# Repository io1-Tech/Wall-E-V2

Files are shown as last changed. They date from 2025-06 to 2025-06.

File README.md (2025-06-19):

# Wall · E V2

This is my personal project, Wall-E, a robot I designed and built from scratch.

It includes electronics, 3D printed parts, servo motors, sound, a laser, and a taser system (for fun). I made everything myself.

Wall-E Robot

## 📦 Project Contents

- `code/`: Arduino code (multiple versions)
- `schematics/`: Schematics, diagrams, and professional circuits
- `3d_models/`: 3D printed designs
- `photos/`: High quality photos of the project
- `sounds/`: Audio effects used in the robot
- `libraries/`: Arduino libraries used in the code
- `components/`: Full Component List

## 🕹️ Control System

This robot can be controlled using:
- Xbox Controller (Bluetooth)
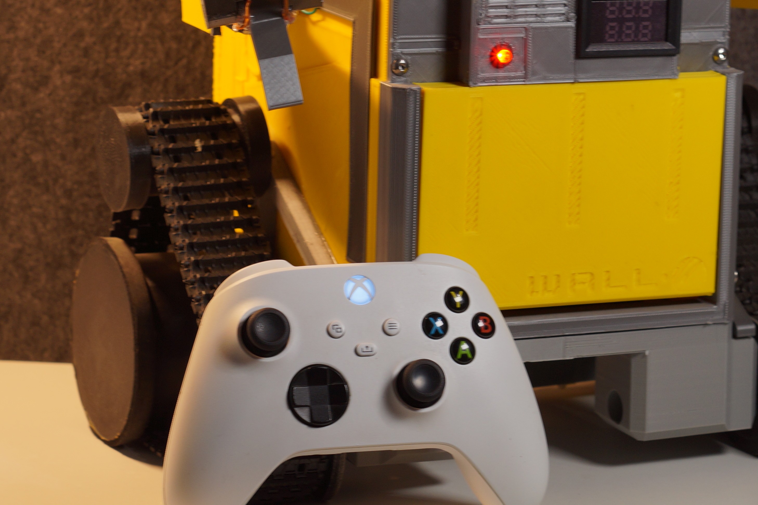
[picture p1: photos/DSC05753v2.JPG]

- Remote XY App (previous versions)
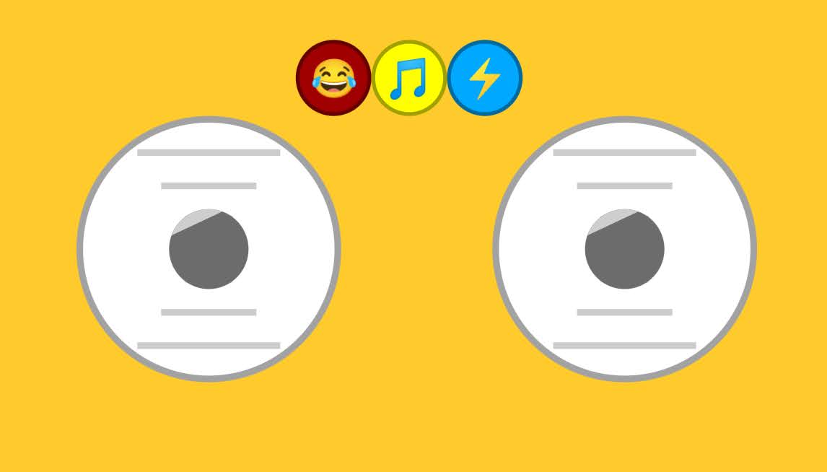
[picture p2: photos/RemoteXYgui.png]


## 🔩 Full Component List

You can find a complete, organized list of all electronic, mechanical, and auxiliary components used in this project in the spreadsheet below:

📄 [Wall-E-V2_components_list.xlsx](components/Wall-E-V2_components_list.xlsx)

This table includes:
- Quantity and part numbers  
- Technical specifications  
- Purpose in project  
- Reason for selection  
- Reference images  

Also i made a schematic with all the conections
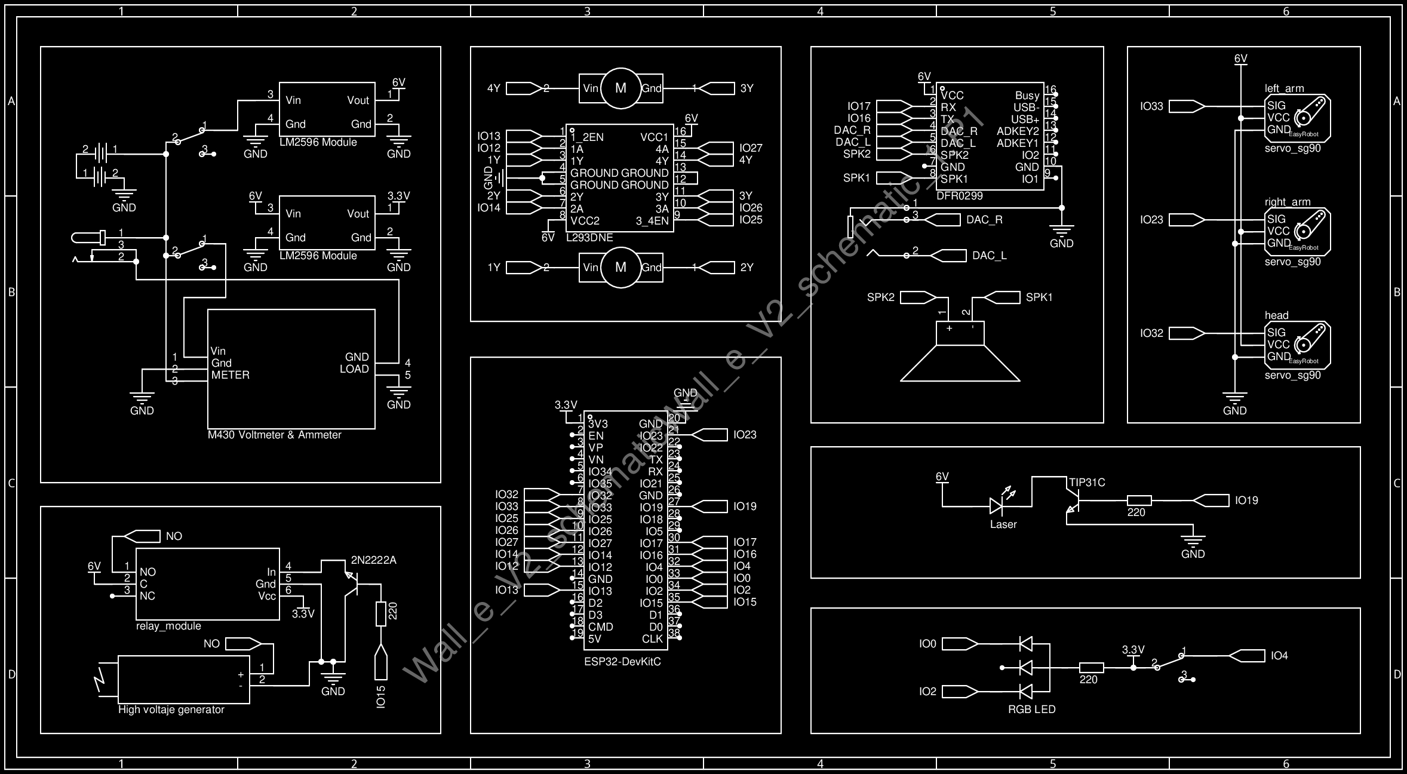
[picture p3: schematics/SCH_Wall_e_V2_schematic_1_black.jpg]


## 🛠️ Tools and Platforms Used

Here’s a list of the main tools and platforms I used throughout the WALL·E project:

- **Fusion 360** – Designed 3D parts of the robot and exported STL files for 3D printing.
- **Fritzing** – Simulated circuits and verified wiring before building the physical prototype.
- **EasyEDA** – Created professional circuit schematics and organized the wiring logic.
- **Arduino IDE** – Developed and uploaded firmware to the ESP32 microcontroller.
- **GitHub** – Used for version control, documentation, and collaboration.
- **OrcaSlicer** – Used slicing all my 3d printabled parts.

## 📸 Preview

Wall-E Robot
Wall-E Robot
Wall-E Robot
Wall-E Robot

## 📂 Version History

- v1.0: Basic control and movement
- v2.8: Bluetooth control with Remote XY
- v3.4: Xbox Controller and sound system added (FINAL VERSION)

## 🧠 Author

Created by: io1

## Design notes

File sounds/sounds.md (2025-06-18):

Place these MP3 files onto a microSD card. Insert the card into the DFPlayer module to enable audio playback in your project.

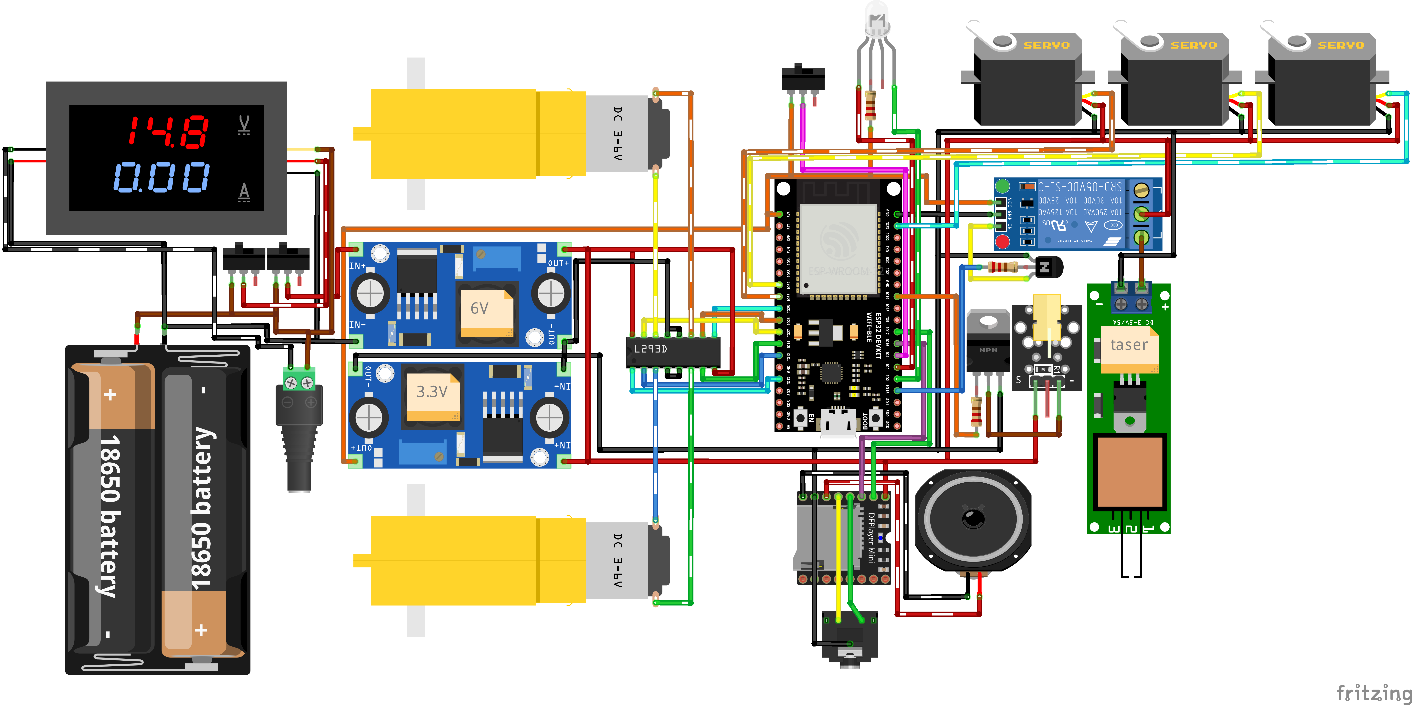
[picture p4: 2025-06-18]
schematics/Fritzing_SCH_Wall_e_V2_schematic.png

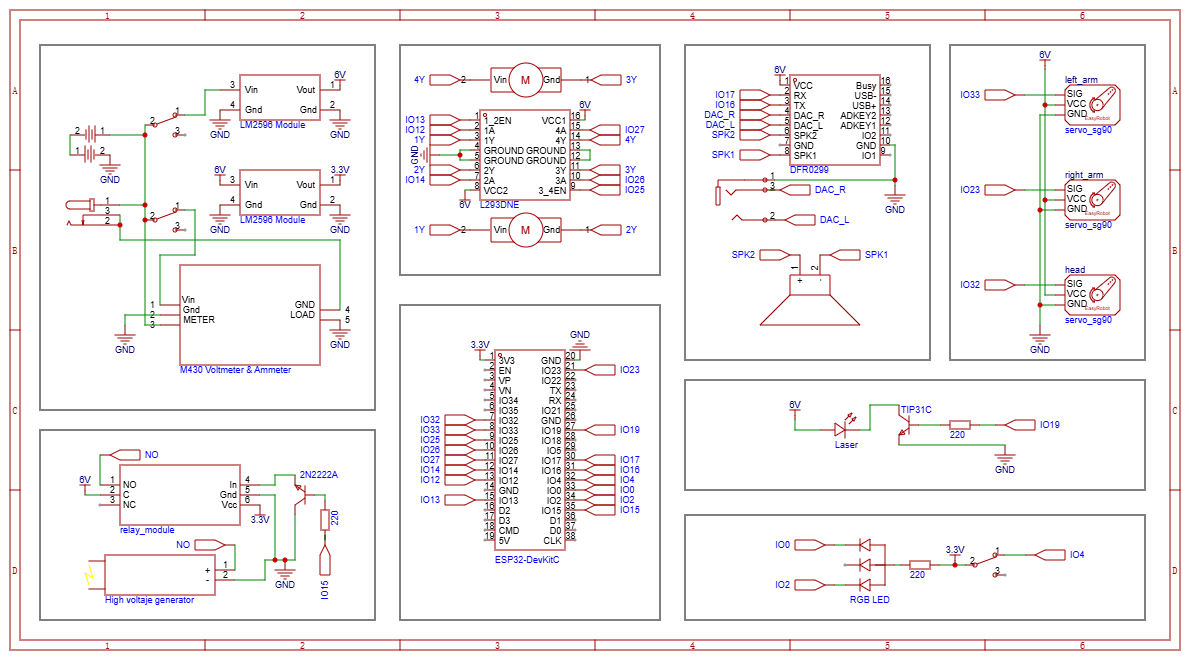
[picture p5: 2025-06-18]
schematics/SCH_Wall_e_V2_schematic_1_normal.png

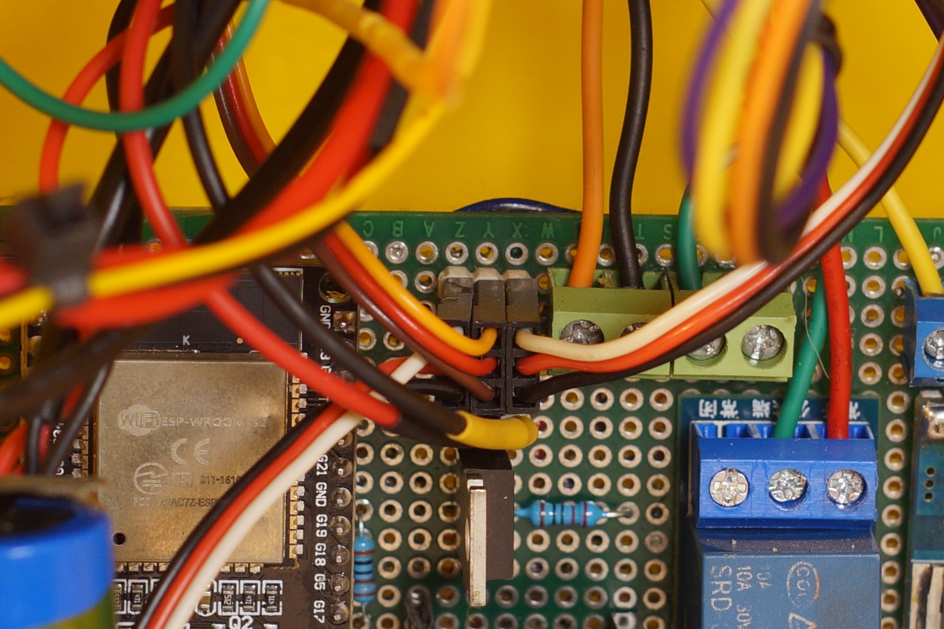
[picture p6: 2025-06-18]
photos/DSC06053v2.JPG

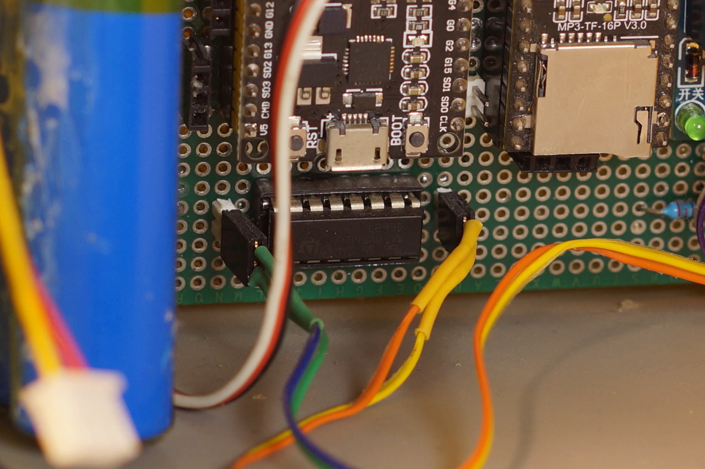
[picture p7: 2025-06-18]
photos/DSC06054v2.JPG

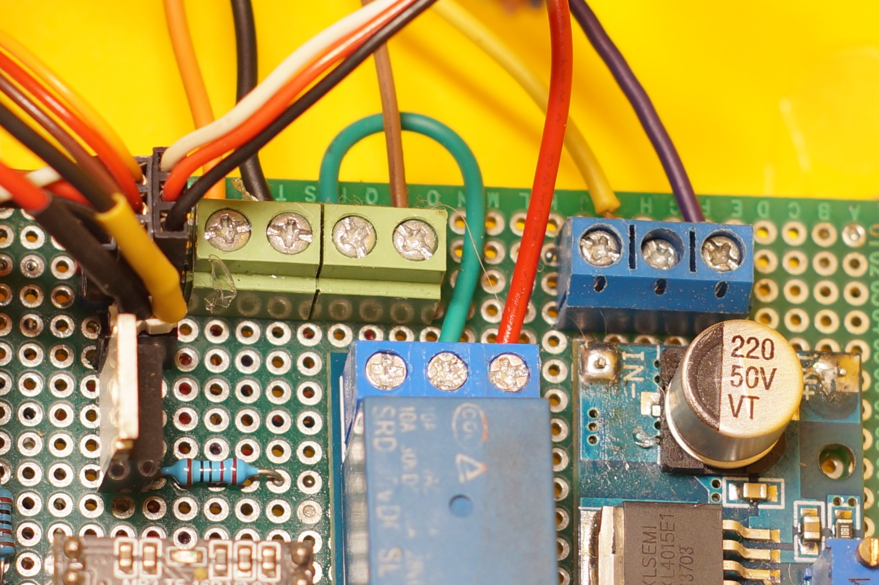
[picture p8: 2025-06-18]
photos/DSC06059v2.JPG

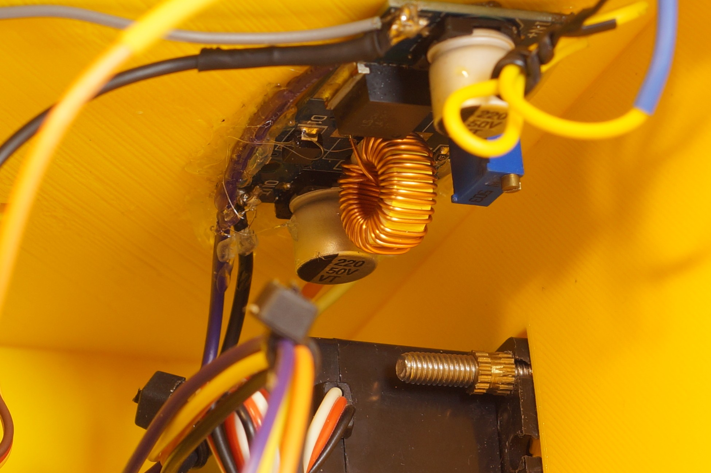
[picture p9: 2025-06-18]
photos/DSC06058v2.JPG

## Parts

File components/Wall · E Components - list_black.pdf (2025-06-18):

# Wall · E Components

Hardware Components | June 2024 | io1 🔩 | Electronics & Control No QTY Component | Description | Function in Project | Why This Component? | Photo

### 1 x1

### ESP-WROOM-32 Dev Board 38pins

Dual-core microcontroller with Wi-Fi & Bluetooth by Espressif. Acts as the central processing unit for all logic, communication, and control tasks.

Acts as the brain of the robot, managing sensor input, motor control, communication, and

logic.

Chosen for its wireless capabilities, performance, and large community. Ideal for embedded robotics.

### 2 x1

### Double H-bridge L293 DIP-16

Dual H-Bridge motor driver capable of driving two DC motors or one stepper motor. Supports bidirectional control.

Drives the left and right DC motors to enable robot

locomotion.

Simple integration with microcontrollers, handles small DC motors efficiently.

### 3 x1

### TIP31C & 2N2222 Transistors

TIP31C: Medium-power NPN BJT, rated for 3A collector current, 40V Vce. 2N2222: Low-power NPN BJT with 800mA max current and fast switching.

TIP31C: Used as a switch for the laser. Receives signal from ESP32 and allows higher current to activate the laser safely. 2N2222: Used to switch the relay for the Taser. Prevented dangerous startup behavior by blocking

Allows safe control of higher loads using GPIO signals.

### 4 x1

### 5V Relay Module (1 channel)

Electromechanical switch that isolates and controls high-voltage circuits using low-voltage control.

Activates the Taser circuit when triggered.

Ensures electrical safety and modularity. Initially problematic, later replaced by transistor system.

### 5 x2

### LM2596 Step- Down Regulator

Step-down voltage regulator, input up

to 35V, output adjustable, 3A max. | Converts 7.4V from battery to 3.3V for logic-level devices and 6V to Motors and High Voltaje Generator

Maintains stable 3.3V for ESP32 and logic circuits from 7.4V Li-ion pack.

### 6 x1

### High Voltage Generator (Taser)

Generates high-voltage pulses (~10kV)

Powers the simulated “Taser” mechanism in the arm. | Mainly for curiosity and add a funny touch :)
🔋 | Power System
No QTY Component | Description | Function in Project | Why This Component? | Photo

### 7 x1

### 18650 Battery Pack (2S1P, 7.4V

### 2200mAh)

Rechargeable lithium-ion battery pack configured as 2 cells in series for 7.4V output.

Provides main power supply for motors, logic, and peripherals.

Provides sufficient capacity and current for both logic and motors.

### 8 x1

### 1A 8.4V Charger

Standard Li-ion battery charger for 2S
(7.4V) configurations. | Recharges the main battery pack. | Matched to battery chemistry and voltage.

### 9 x1

### M430 Voltmeter & Ammeter

Measures and displays real-time voltage and current of the power supply.

Monitors battery status and power draw.

Prevents undervoltage and ensures safe operation.

⚙ | Mechanical Actuation & Movement No QTY Component | Description | Function in Project | Why This Component? | Photo

10

### SG90 Micro Servo (Head)

Compact analog servo with ~180° movement range, low power consumption.

Controls lightweight parts like the neck articulation.

Budget-friendly and sufficient for one head. Future upgrade required.

11

### MG996R Servo (Arms)

High-torque digital servo with metal gears, rotation of ~180°, operating at 4.8–7.2V.

Controls the arm movement

for expression and motion. Chosen for torque, accessibility and capacity, though near operational limit. Future upgrade required.

12

### Yellow Gear Motors (L-shaped)

Main movement system | Main movement system. Future upgrade required.

Low-cost motors with adequate torque. Limited for heavy load.

13

### Plastic Track System

Pre-assembled plastic track mechanism with wheels.

Provides traction, but due to poor fit, not fully
functional.

Bought pre-assembled for ease; unfortunately, poorly designed, with wheels often slipping out.

🖌 | 3D Design & Materials
No QTY Component | Description | Function in Project | Why This Component? | Photo

14

### Fusion 360 Design

Autodesk Fusion is a commercial computer-aided design (CAD), has built-in capabilities for 3D modeling, collaboration, simulation and documentation.

Used to Design WALL·E’s body, arms, and head components.

Ensures accurate fit, modularity, and presentation quality.

15

### PLA Filament

(Black, Yellow,

### Silver)

Thermoplastic material used for 3D printing parts. | Used to print WALL·E’s body, arms, and head components.

Lightweight, good finish, and easy to post- process.

16

### M4 Brass Inserts

Brass components used to reinforce screw holes in 3D printed parts. Provides stronger and
reusable screw threading in PLA pieces.

Avoids plastic cracking and adds professionalism.

💡 | Auxiliary & Visual Effects
No QTY Component | Description | Function in Project | Why This Component? | Photo

17

### DFPlayer Mini

MP3 audio playback module with onboard microSD and speaker support.

Plays sound effects or voice commands from WALL·E.

Allows autonomous sound effects stored on microSD.

18

### 5mm Laser Diode (Red)

Compact red diode laser module operating at 5V.

Aesthetic effect used in the arm for visual targeting. Aesthetic enhancement and directional indicator.

19

### RGB LED (Common Anode)

Multi-color LED with 4 pins: one common anode and R/G/B cathodes.

Indicates Safe mode, green for safe, red for taser activated

For simplicity and a lot of documentation online

### 20 x3

### DPDT Switch

Double Pole Double Throw switch with two stable ON states.

Ensures manual override for safe operation.

A classic Switch

21

### 4Ohm 3W speaker

Audio playback speaker, conected to DF player mini

Audio output for Sound effects and music | Maximum power and resistance supported by the DF player mini

22

### Xbox Series Controller

Wireless Bluetooth gamepad compatible with ESP32 via BLE. Offers analog and digital input.

Used as the remote controller to wirelessly operate WALL·E's movement and

features.

Chosen for its BLE compatibility, precision, and ergonomic design. Easy to integrate and

intuitive for real-time control.

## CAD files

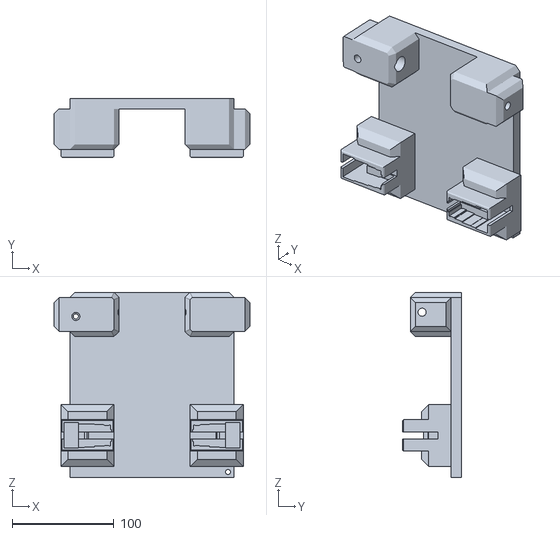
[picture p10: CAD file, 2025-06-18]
3d_models/stl files/Down_side.stl
192.5 x 57.6 x 182.0

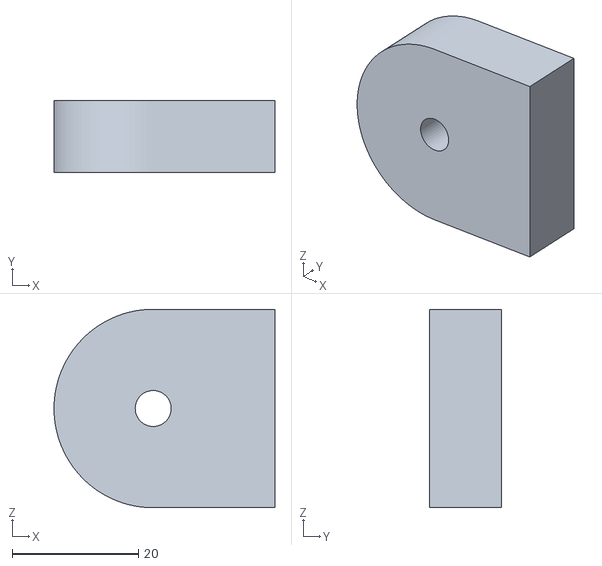
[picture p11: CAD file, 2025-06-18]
3d_models/stl files/Shoulder_r.stl
35.0 x 11.4 x 31.5

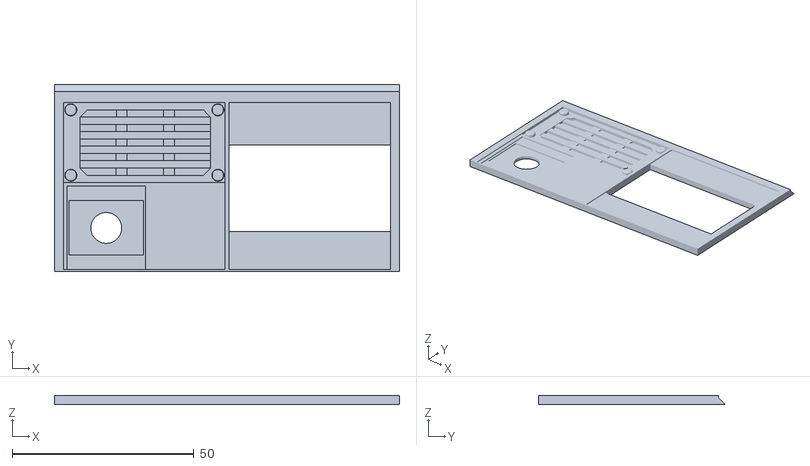
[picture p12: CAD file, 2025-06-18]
3d_models/stl files/Dock.stl
95.0 x 51.5 x 2.50

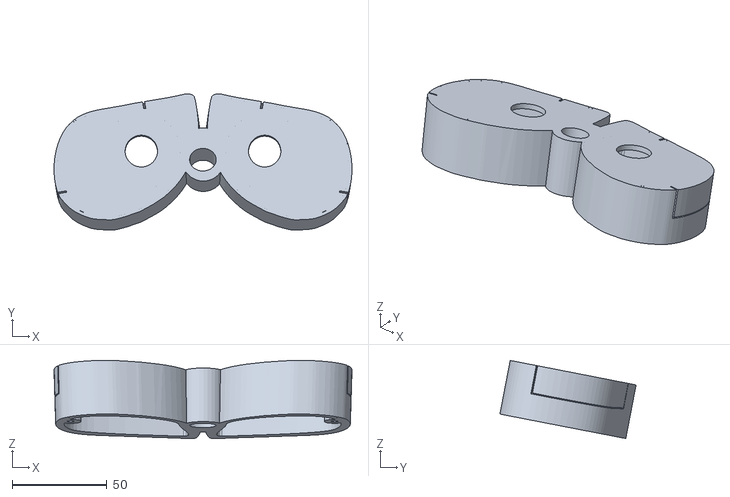
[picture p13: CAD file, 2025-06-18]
3d_models/stl files/Eyes_back.stl
157.0 x 71.8 x 41.2

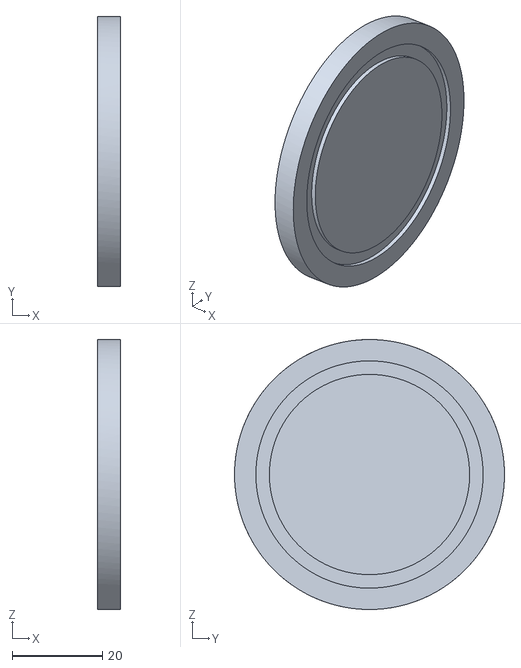
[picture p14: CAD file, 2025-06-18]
3d_models/stl files/Front_wheel_left_cover.stl
5.00 x 60.0 x 60.0

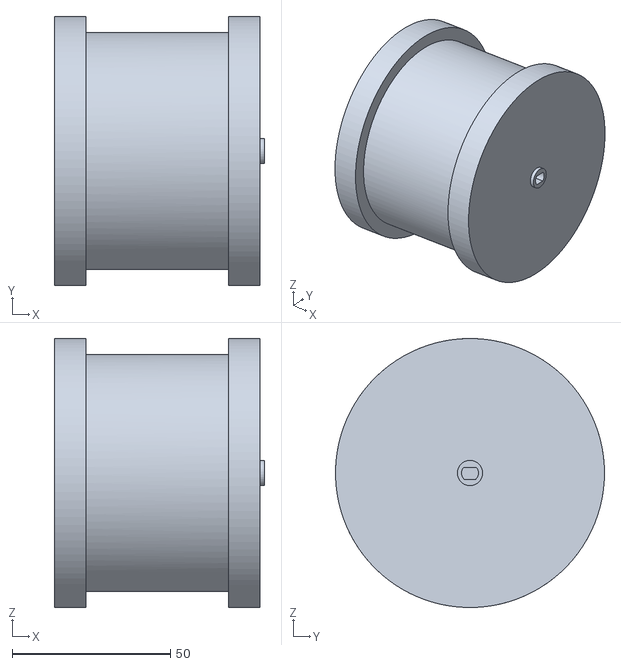
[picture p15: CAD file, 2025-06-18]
3d_models/stl files/Back_wheel_left.stl
66.5 x 85.0 x 85.0

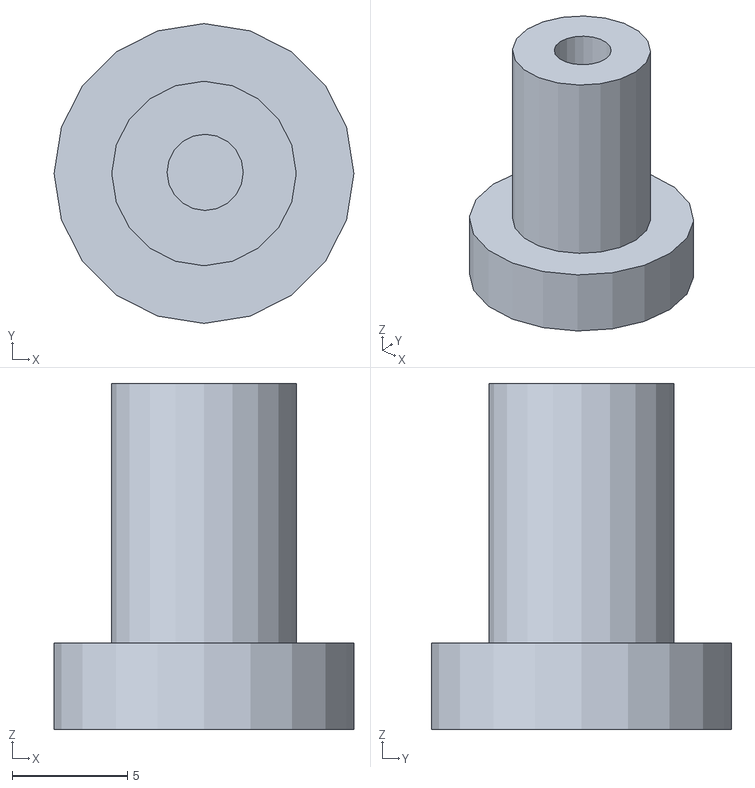
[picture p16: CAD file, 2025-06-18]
3d_models/stl files/Separador PCB.stl
13.0 x 13.0 x 15.0

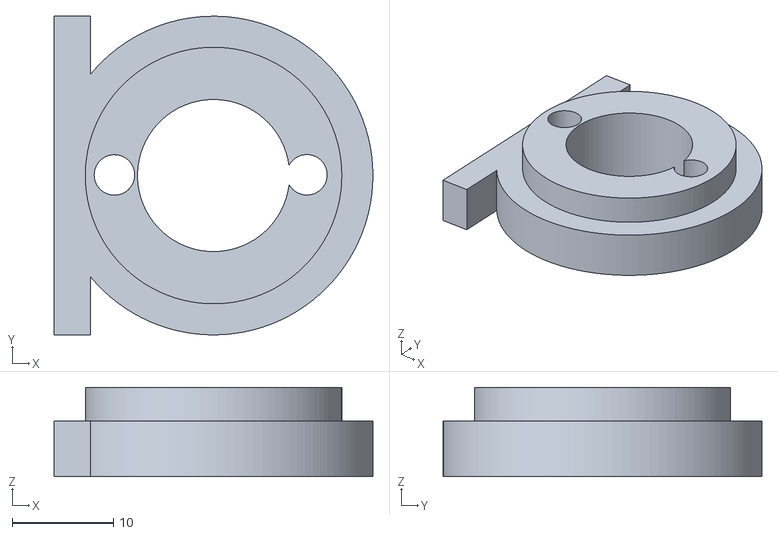
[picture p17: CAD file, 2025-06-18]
3d_models/stl files/Wrist_r_2.0.stl
31.4 x 31.5 x 8.80

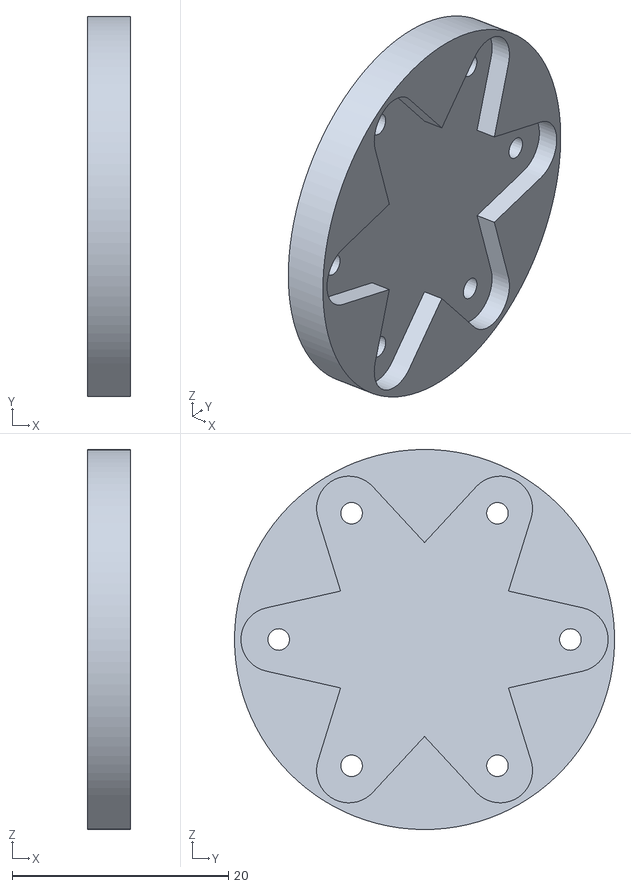
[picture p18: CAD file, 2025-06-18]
3d_models/stl files/Bodydasd.stl
4.00 x 35.2 x 35.2

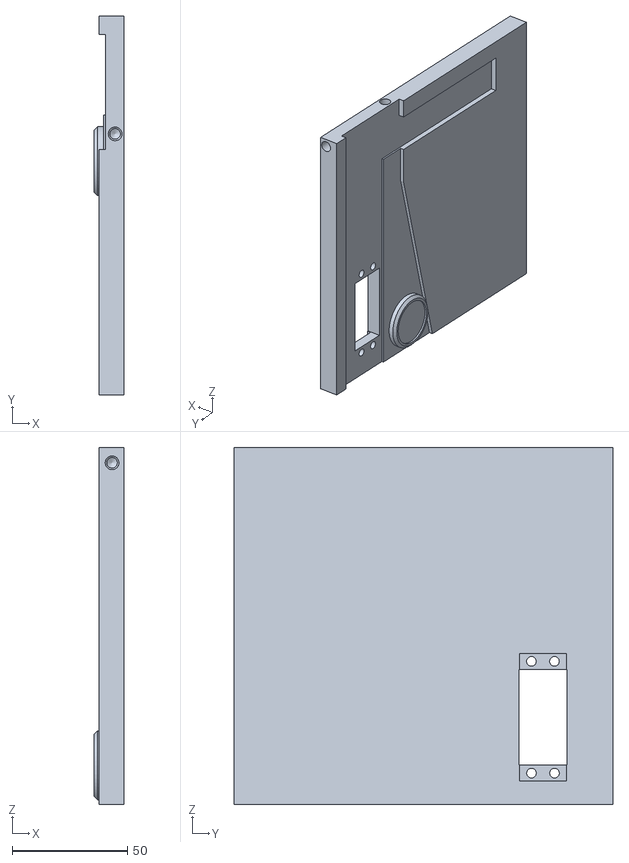
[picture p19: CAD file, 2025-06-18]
3d_models/stl files/Right_Side.stl
12.9 x 164.5 x 155.0

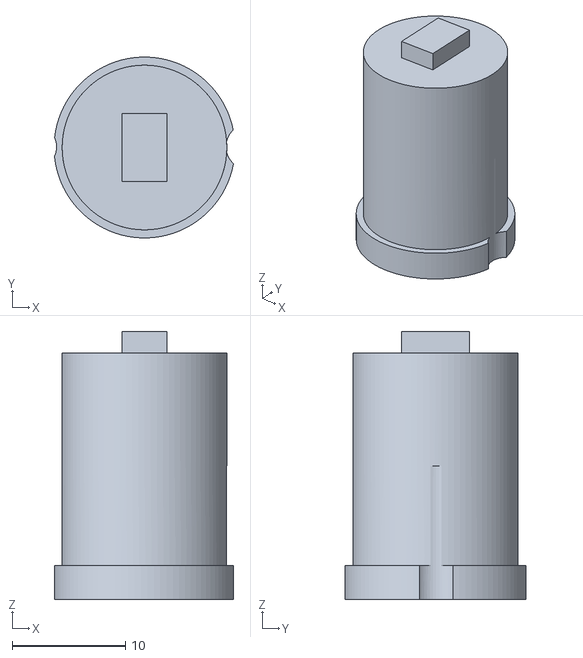
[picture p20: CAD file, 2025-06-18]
3d_models/stl files/Wrist_2_r_3.0.stl
15.8 x 16.0 x 23.7

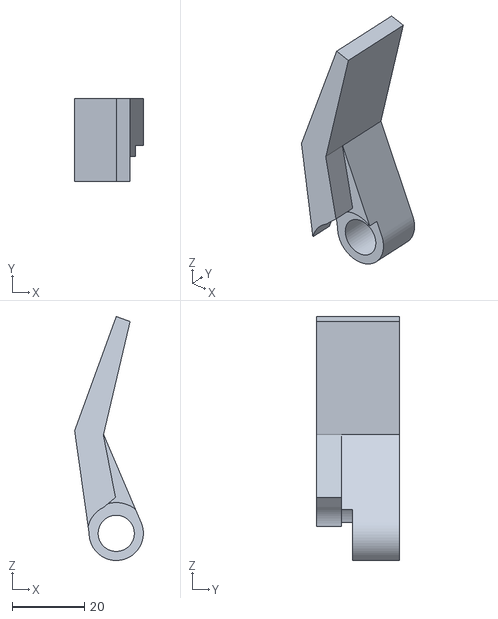
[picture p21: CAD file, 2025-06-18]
3d_models/stl files/Finger_2_r.stl
19.0 x 23.0 x 67.4

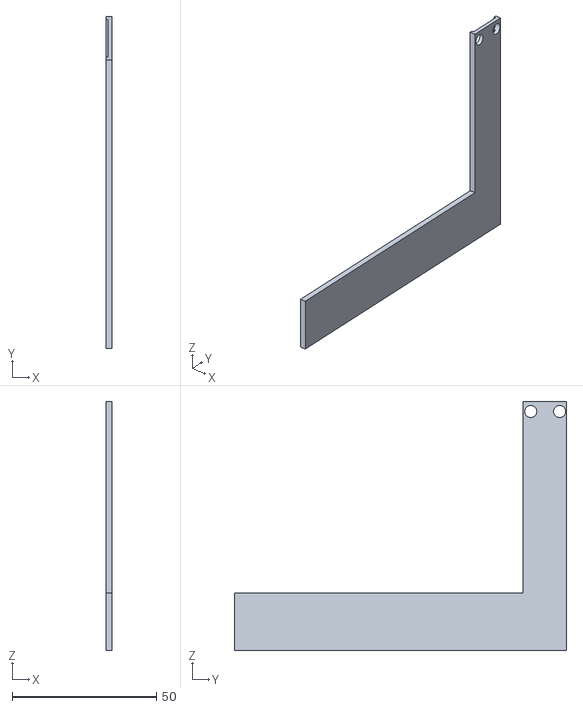
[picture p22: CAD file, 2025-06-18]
3d_models/stl files/Bodyfiopgsioñufv.stl
2.25 x 115.0 x 86.4

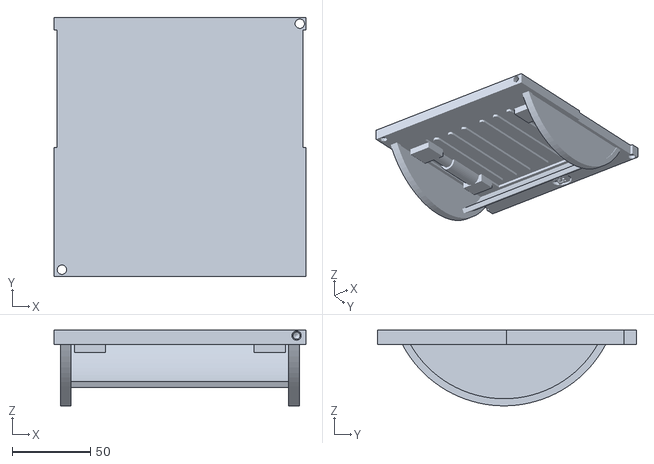
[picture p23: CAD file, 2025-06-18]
3d_models/stl files/Back.stl
161.2 x 165.5 x 48.3

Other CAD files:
3d_models/stl files/Thumb_r.stl
3d_models/stl files/Wrist_3_r.stl
3d_models/stl files/Motor_support_left.stl
3d_models/stl files/Back_head_2.0.stl
3d_models/stl files/Back_wheel_left (2).stl
3d_models/stl files/Back_wheel_left(3).stl
3d_models/stl files/Back_wheel_left_(2).stl
3d_models/stl files/Body1.stl
3d_models/stl files/Eyes_front.stl
3d_models/stl files/Finger_1_r.stl
3d_models/stl files/Front_wheel_left.stl
3d_models/stl files/Neck_adapter 2.0.stl
3d_models/stl files/Neck_left.stl
3d_models/stl files/Neck_right.stl
3d_models/stl files/Right_Side_2.stl
3d_models/stl files/Right_arm_2.0.stl
3d_models/stl files/Top.stl
3d_models/stl files/Top_wheel_left.stl
3d_models/stl files/Top_wheel_left_cover.stl
3d_models/stl files/Wrist_4_r.stl

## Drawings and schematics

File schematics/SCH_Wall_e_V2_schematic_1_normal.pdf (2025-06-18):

# TIP31C Wall_e_V2_schematicWall_e_V2_schematic_1.P1

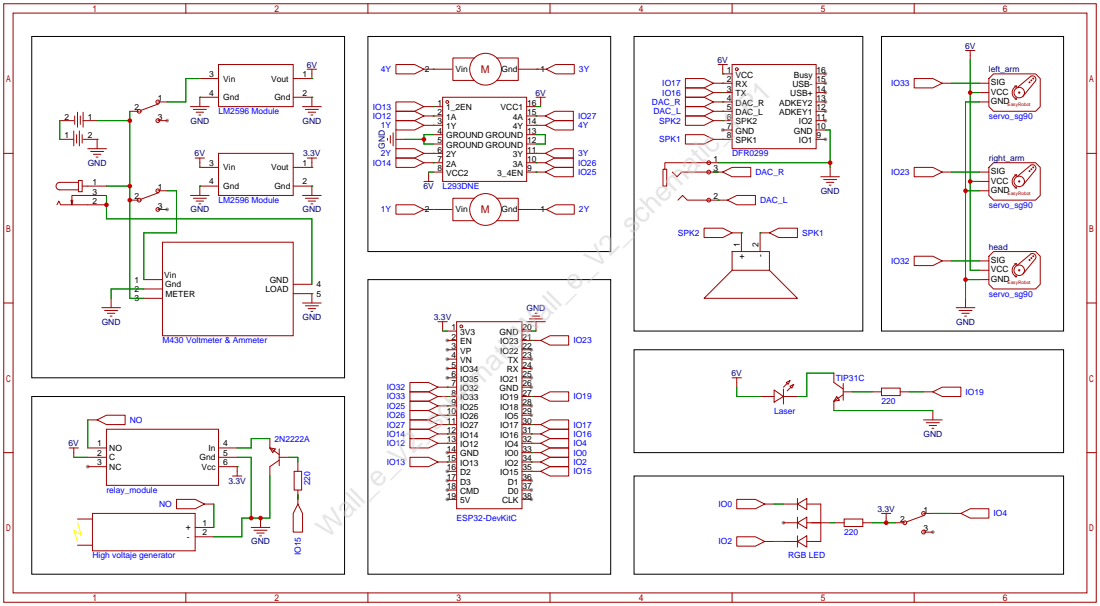
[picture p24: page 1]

GND 10 IO2 11 ADKEY1 12 ADKEY2 13 USB+ 14 USB- 15 Busy 16

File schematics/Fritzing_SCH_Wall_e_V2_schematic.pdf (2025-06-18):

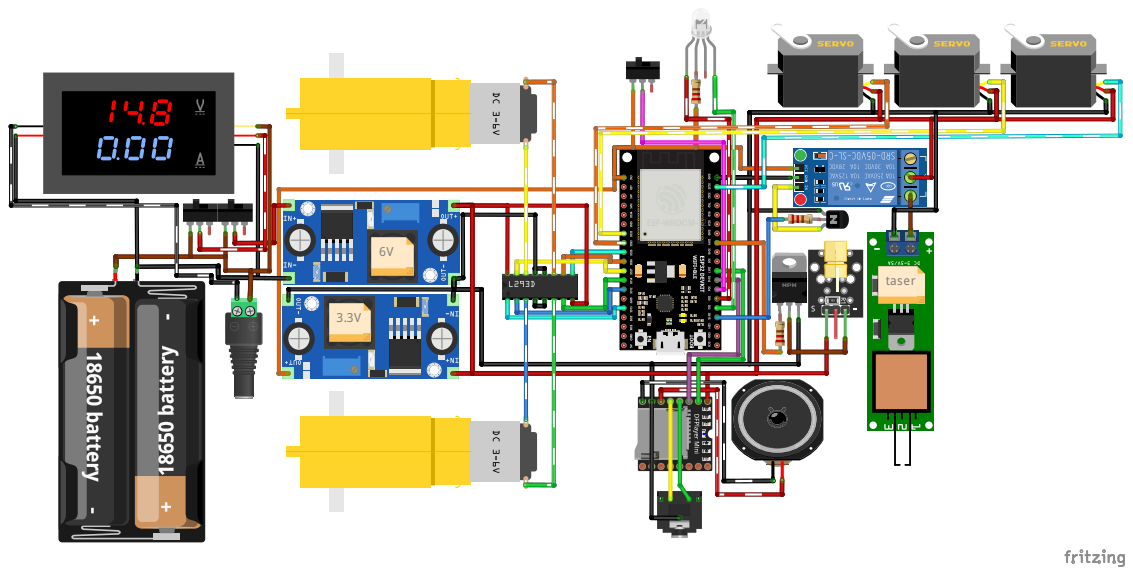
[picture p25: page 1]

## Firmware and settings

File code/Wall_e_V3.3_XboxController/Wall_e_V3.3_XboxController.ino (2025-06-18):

/////////////////////////////////
/////////////////////////////////
////   CODED BY NICOLÁS      ////
/////////////////////////////////
/////////////////////////////////

// INITIALIZE 🔴🟢🔵 RGB LED //

int redPin = 15;
int greenPin = 2;
int pinIn = 4;
int volVal;

/////////////////////////////////

// INITIALIZE LAZER 💥 //

int laser = 19;

//////////////////////////

// 🎵 INITIALIZE DFPLAYER //

#include <DFRobotDFPlayerMini.h>
#include "Arduino.h"
#define FPSerial Serial1
DFRobotDFPlayerMini myDFPlayer;

/////////////////////////////

// 🦾 INITIALIZE SERVOS //

#include <ESP32Servo.h>

const int pinServo1 = 23; // right_arm
int servoVal1;
const int pinServo2 = 33; // left_arm
int servoVal2;
const int pinServo3 = 32; // Head servo
int servoValR3;
int servoValL3;

Servo miServo1;
Servo miServo2;
Servo miServo3;

/////////////////////////

// 🎮 INITIALIZE XBOX REMOTE //

#include <XboxSeriesXControllerESP32_asukiaaa.hpp>
XboxSeriesXControllerESP32_asukiaaa::Core xboxController;
XboxSeriesXHIDReportBuilder_asukiaaa::ReportBase repo;

////////////////////////////////

// 💪 VARIABLES //

  int xVal1;
  int yVal1;
  int xVal2;
  int yVal2;
  int emoteButtonVal;
  int musicButtonVal;
  bool reverseState = false;

  int motor1Pin1 = 12;
  int motor1Pin2 = 14;
  int motor2Pin1 = 27;
  int motor2Pin2 = 26;
  int enablePin1 = 13;
  int enablePin2 = 25;

  int relayPin = 18;

  int busyVal;

/////////////////////////

/*💀*/ void setup() //////////////////////////////////////
{
// 🎮 INITIALIZE XBOX REMOTE // 

  Serial.begin(115200);
  Serial.println("Starting NimBLE Client");
  xboxController.begin();

/////////////////////////
  
// 🐧 INITIALIZE PINS //
  
  pinMode(motor1Pin1, OUTPUT);
  pinMode(motor1Pin2, OUTPUT);
  pinMode(motor2Pin1, OUTPUT);
  pinMode(motor2Pin2, OUTPUT);
  pinMode(enablePin2, OUTPUT);
  pinMode(enablePin1, OUTPUT);
  pinMode(relayPin, OUTPUT);
  pinMode(pinServo3, OUTPUT);

/////////////////////////

// 🦾 INITIALIZE SERVOS //

  miServo1.setPeriodHertz(50); // Establecer la frecuencia en 50 Hz (estándar para servos)
  miServo1.attach(pinServo1, 500, 2400); // Configurar el pin del servo y los límites del pulso

  miServo2.setPeriodHertz(50); // Establecer la frecuencia en 50 Hz (estándar para servos)
  miServo2.attach(pinServo2, 500, 2400); // Configurar el pin del servo y los límites del pulso

  miServo3.setPeriodHertz(50); // Establecer la frecuencia en 50 Hz (estándar para servos)
  miServo3.attach(pinServo3, 500, 2400); // Configurar el pin del servo y los límites del pulso

/////////////////////////

// 🎵 DFPLAYER //
 
#if (defined ESP32)
  FPSerial.begin(9600, SERIAL_8N1, /*rx =*/16, /*tx =*/17);
#else
  FPSerial.begin(9600);
#endif

  Serial.begin(115200);

  Serial.println();
  Serial.println(F("DFRobot DFPlayer Mini Demo"));
  Serial.println(F("Initializing DFPlayer ... (May take 3~5 seconds)"));
  
  if (!myDFPlayer.begin(FPSerial, /*isACK = */true, /*doReset = */true)) {  //Use serial to communicate with mp3.
    Serial.println(F("Unable to begin:"));
    Serial.println(F("1.Please recheck the connection!"));
    Serial.println(F("2.Please insert the SD card!"));
    while(true){
      delay(0); // Code to compatible with ESP8266 watch dog.
    }
  }
  Serial.println(F("DFPlayer Mini online."));
  
myDFPlayer.volume(20);
myDFPlayer.play(1);

/////////////////////////

// INITIALIZE 🔴🟢🔵 RGB LED //

pinMode(redPin, OUTPUT);
pinMode(greenPin, OUTPUT);
pinMode(pinIn, INPUT);

/////////////////////////////////

// INITIALIZE LASER 💥 //

pinMode(laser, OUTPUT);

//////////////////////////

}

/*💀*/  void loop() //////////////////////////////////////
{
// 🎮 XBOX REMOTE //

  xboxController.onLoop();
  if (xboxController.isConnected()) {
    if (xboxController.isWaitingForFirstNotification()) {
      Serial.println("waiting for first notification");
    } else {
      Serial.println("Address: " + xboxController.buildDeviceAddressStr());
      Serial.print(xboxController.xboxNotif.toString());
      unsigned long receivedAt = xboxController.getReceiveNotificationAt();
      uint16_t joystickMax = XboxControllerNotificationParser::maxJoy;
      Serial.print("joyLHori rate: ");
      Serial.println((float)xboxController.xboxNotif.joyLHori / joystickMax);
      Serial.print("joyLVert rate: ");
      Serial.println((float)xboxController.xboxNotif.joyLVert / joystickMax);
      Serial.print("joyRHori rate: ");
      Serial.println((float)xboxController.xboxNotif.joyRHori / joystickMax);
      Serial.print("joyRVert rate: ");
      Serial.println((float)xboxController.xboxNotif.joyRVert / joystickMax);
      Serial.println("battery " + String(xboxController.battery) + "%");
      Serial.println("received at " + String(receivedAt));
    }
  } else {
    Serial.println("not connected");
    if (xboxController.getCountFailedConnection() > 2) {
      ESP.restart();
    }
  }
  Serial.println("at " + String(millis()));
  delay(0);

////////////////////

// ⚡ TASER CONTROL //

if (xboxController.xboxNotif.btnRS == 1 && xboxController.xboxNotif.btnLS == 1 && volVal == 1) {
    digitalWrite(relayPin, HIGH);
  }  
else {
    digitalWrite(relayPin, LOW);
  }

/////////////////////////

// 🎵 DFPLAYER CONTROL //

 if (xboxController.xboxNotif.btnA != 0) {
  int numero = random(1, 4);
  myDFPlayer.play(numero);
 }

 if (xboxController.xboxNotif.btnB != 0) { 
  myDFPlayer.play(5);
 }

 if (xboxController.xboxNotif.btnB != 0 && busyVal != 0){
  myDFPlayer.pause();
 }

 busyVal = myDFPlayer.readState();

/////////////////////////

// 🦾 SERVO CONTROL //

servoValR3 = map(xboxController.xboxNotif.trigRT, 0, 1023, 90, 0);
servoValL3 = map(xboxController.xboxNotif.trigLT, 0, 1023, 90, 180);
if(xboxController.xboxNotif.trigRT != 0)
{
  miServo3.write(servoValR3);
}
if(xboxController.xboxNotif.trigLT != 0)
{
  miServo3.write(servoValL3);
}
else if (xboxController.xboxNotif.trigLT == 0 && xboxController.xboxNotif.trigRT == 0)
{
  miServo3.write(90);
}

servoVal1 = map(xboxController.xboxNotif.joyLVert, 0, 65535, 180, 60);
miServo1.write(servoVal1);

servoVal2 = map(xboxController.xboxNotif.joyRVert, 0, 65535, 58, 180);
miServo2.write(servoVal2);

/////////////////////////

// 🔴🟢🔵 RGB LED //

volVal = digitalRead(pinIn);
Serial.println(volVal);

if(volVal == 1)
  {
    digitalWrite(redPin, LOW);
    digitalWrite(greenPin, HIGH);
  } 
if(volVal == 0)
  {
    digitalWrite(redPin, HIGH);
    digitalWrite(greenPin, LOW);
  } 

//////////////////////

// LASER 💥 //

if(xboxController.xboxNotif.btnY == 1)
{
 digitalWrite(laser, HIGH);
}
else
{
  digitalWrite(laser, LOW);
}
//////////////////////////

// 🚗 MOTOR CONTROL: //
 
 if(xboxController.xboxNotif.btnX == 1)
 {
  reverseState = !reverseState;
 }

 if(xboxController.xboxNotif.btnRB == 0 && xboxController.xboxNotif.btnLB == 0){
    digitalWrite(motor1Pin1, LOW);
    digitalWrite(motor1Pin2, LOW);
    digitalWrite(motor2Pin1, LOW);
    digitalWrite(motor2Pin2, LOW);
    digitalWrite(enablePin1, LOW);
    digitalWrite(enablePin2, LOW);
  }

 if(xboxController.xboxNotif.btnRB != 0 && xboxController.xboxNotif.btnLB == 0){
   digitalWrite(enablePin1, HIGH);
   digitalWrite(motor1Pin1, HIGH);
   digitalWrite(motor1Pin2, LOW);
   digitalWrite(motor2Pin1, LOW);
   digitalWrite(motor2Pin2, HIGH);
   digitalWrite(enablePin2, HIGH);
    repo.v.select.right = false;
    repo.v.select.shake = true;
    repo.v.power.shake = 10;
    xboxController.writeHIDReport(repo);
   }

 if(xboxController.xboxNotif.btnLB != 0 && xboxController.xboxNotif.btnRB == 0){
   digitalWrite(enablePin1, HIGH);
   digitalWrite(motor1Pin1, LOW);
   digitalWrite(motor1Pin2, HIGH);
   digitalWrite(motor2Pin1, HIGH);
   digitalWrite(motor2Pin2, LOW);
   digitalWrite(enablePin2, HIGH);
    repo.v.select.right = false;
    repo.v.select.shake = true;
    repo.v.power.shake = 10;
    xboxController.writeHIDReport(repo);
   }

 if(xboxController.xboxNotif.btnRB != 0 && xboxController.xboxNotif.btnLB != 0 && reverseState == false){
   digitalWrite(enablePin1, HIGH);
   digitalWrite(motor1Pin1, HIGH);
   digitalWrite(motor1Pin2, LOW);
   digitalWrite(motor2Pin1, HIGH);
   digitalWrite(motor2Pin2, LOW);
   digitalWrite(enablePin2, HIGH);
    repo.v.select.right = false;
    repo.v.select.shake = true;
    repo.v.power.shake = 10;
    xboxController.writeHIDReport(repo);
   }

 if(xboxController.xboxNotif.btnRB != 0 && xboxController.xboxNotif.btnLB != 0 && reverseState == true){
   digitalWrite(enablePin1, HIGH);
   digitalWrite(motor1Pin1, LOW);
   digitalWrite(motor1Pin2, HIGH);
   digitalWrite(motor2Pin1, LOW);
   digitalWrite(motor2Pin2, HIGH);
   digitalWrite(enablePin2, HIGH);
    repo.v.select.right = false;
    repo.v.select.shake = true;
    repo.v.power.shake = 10;
    xboxController.writeHIDReport(repo);
   }
/////////////////////////

}

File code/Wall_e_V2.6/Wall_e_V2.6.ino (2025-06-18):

/////////////////////////////
//   CODED BY NICOLÁS 🗿  //
/////////////////////////////

// 🕹️ INICIALIZAR REMOTEXY //

#define REMOTEXY_MODE__ESP32CORE_BLUETOOTH
#include <BluetoothSerial.h>
#include <RemoteXY.h>
#define REMOTEXY_BLUETOOTH_NAME "Wall-e"
#pragma pack(push, 1)
uint8_t RemoteXY_CONF[] =   // 69 bytes
  { 255,7,0,0,0,59,0,16,79,0,1,0,34,6,10,10,34,31,240,159,
  152,130,0,1,0,44,6,10,10,94,31,240,159,142,181,0,5,32,5,16,
  35,35,27,31,31,5,32,60,16,35,35,27,31,31,1,0,54,6,10,10,
  177,31,226,154,161,0 };
struct {
  uint8_t emote_1; // =1 if button pressed, else =0 
  uint8_t emote_2; // =1 if button pressed, else =0 
  int8_t joystick_1_x; // from -100 to 100  
  int8_t joystick_1_y; // from -100 to 100  
  int8_t joystick_2_x; // from -100 to 100  
  int8_t joystick_2_y; // from -100 to 100  
  uint8_t emote_3; // =1 if button pressed, else =0 
 
  uint8_t connect_flag;  // =1 if wire connected, else =0 

} RemoteXY;
#pragma pack(pop)

/////////////////////////

// 🦾 INICIALIZAR SERVOS //

#include <ESP32Servo.h>

const int pinServo1 = 33; // Puedes cambiar este valor según la conexión física
int servoVal1;
const int pinServo2 = 32; // Puedes cambiar este valor según la conexión física
int servoVal2;
const int pinServo3 = 23; // Puedes cambiar este valor según la conexión física
int servoVal3;

Servo miServo1;
Servo miServo2;
Servo miServo3;

/////////////////////////

// 💪 VARIABLES //

  int xVal1;
  int yVal1;
  int xVal2;
  int yVal2;
  int emoteButtonVal;
  int musicButtonVal;
  int shockButtonVal;

  int motor1Pin1 = 12;
  int motor1Pin2 = 14;
  int motor2Pin1 = 27;
  int motor2Pin2 = 26;
  int enablePin1 = 13;
  int enablePin2 = 25;

/////////////////////////

/*💀*/ void setup() //////////////////////////////////////
{
// 🕹️ INICIALIZAR REMOTEXY // 

  RemoteXY_Init (); 
  Serial.begin(9600);

/////////////////////////

// 🦾 INICIALIZAR SERVOS //

  miServo1.setPeriodHertz(100); // Establecer la frecuencia en 50 Hz (estándar para servos)
  miServo1.attach(pinServo1, 500, 2400); // Configurar el pin del servo y los límites del pulso

  miServo2.setPeriodHertz(100); // Establecer la frecuencia en 50 Hz (estándar para servos)
  miServo2.attach(pinServo2, 500, 2400); // Configurar el pin del servo y los límites del pulso

  miServo3.setPeriodHertz(100); // Establecer la frecuencia en 50 Hz (estándar para servos)
  miServo3.attach(pinServo3, 500, 2400); // Configurar el pin del servo y los límites del pulso

/////////////////////////

// 🚗 MOTORES //
  
  pinMode(motor1Pin1, OUTPUT);
  pinMode(motor1Pin2, OUTPUT);
  pinMode(motor2Pin1, OUTPUT);
  pinMode(motor2Pin2, OUTPUT);
  pinMode(enablePin2, OUTPUT);
  pinMode(enablePin1, OUTPUT);

/////////////////////////
}

/*💀*/  void loop() //////////////////////////////////////
{

RemoteXY_Handler ();
  
// 🗿 ESCRITURA DE VARIABLES //

  xVal1 = RemoteXY.joystick_1_x;
  yVal1 = RemoteXY.joystick_1_y;
  xVal2 = RemoteXY.joystick_2_x;
  yVal2 = RemoteXY.joystick_2_y;

  emoteButtonVal = RemoteXY.emote_1;
  musicButtonVal = RemoteXY.emote_2;
  shockButtonVal = RemoteXY.emote_3;
  
  Serial.print("Joystick 1 X: ");
  Serial.print(xVal1);

  Serial.print("   Joystick 1 Y: ");
  Serial.print(yVal1);

  Serial.print("       Joystick 2 X: ");
  Serial.print(xVal2);

  Serial.print("   Joystick 2 Y: ");
  Serial.print(yVal2);

  Serial.print("         Emote Button: ");
  Serial.print(emoteButtonVal);

  Serial.print("   Music Button: ");
  Serial.print(musicButtonVal);

  Serial.print("   Shock Button: ");
  Serial.println(shockButtonVal);

/////////////////////////

// 🚗 CONTROL DE MOTORES: //

// ❌ DETENER MOTORES //
if(xVal1 == 0){
digitalWrite(enablePin1,LOW);
digitalWrite(enablePin2,LOW);
}


// ⬆️⬇️ ARRIBA Y ABAJO //
 if(yVal1 == 100){
digitalWrite(motor1Pin1, LOW);
digitalWrite(motor1Pin2, HIGH);
digitalWrite(motor2Pin1, LOW);
digitalWrite(motor2Pin2, HIGH);
digitalWrite(enablePin2,HIGH);
digitalWrite(enablePin1,HIGH);
  }

if(yVal1 == -100){
digitalWrite(motor1Pin1, HIGH);
digitalWrite(motor1Pin2, LOW);
digitalWrite(motor2Pin1, HIGH);
digitalWrite(motor2Pin2, LOW);
digitalWrite(enablePin1,HIGH);
digitalWrite(enablePin2,HIGH);

  }


// ➡️⬅️ DERECHA E IZQUIERDA //
if(xVal1 == 100){
digitalWrite(motor1Pin1, HIGH);
digitalWrite(motor1Pin2, LOW);
digitalWrite(motor2Pin1, LOW);
digitalWrite(motor2Pin2, HIGH);
digitalWrite(enablePin1,HIGH);
digitalWrite(enablePin2,HIGH);

  }

if(xVal1 == -100){
digitalWrite(motor1Pin1, LOW);
digitalWrite(motor1Pin2, HIGH);
digitalWrite(motor2Pin1, HIGH);
digitalWrite(motor2Pin2, LOW);
digitalWrite(enablePin1,HIGH);
digitalWrite(enablePin2,HIGH);

  }

/////////////////////////

// 🦾 CONTROL DE SERVOS //

servoVal1 = map(yVal2, 100, -100, 0, 115);
miServo1.write(servoVal1);
servoVal2 = map(yVal2, 100, -100, 180, 58);
miServo2.write(servoVal2);
servoVal3 = map(xVal2, 100, -100, 180, 0);
miServo3.write(servoVal3);

/////////////////////////

}
